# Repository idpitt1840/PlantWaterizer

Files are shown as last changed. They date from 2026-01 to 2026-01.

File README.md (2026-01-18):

An ESPHome / Home Assistant Indoor plant irrigation system

This unit monitors the moisture content of up to 5 plant pots and delivers water to them as needed.  It uses low cost moisture sensors and pumps. 



( The controller is the top box.  The bottom box is an overengineered grow light power switch that's repurposed from a different project ).



The pots are fed via a 3D printed water distribution ring ( STLs available from https://www.printables.com/model/103003-drip-irrigation-ring ). I modified the design a little to take a bigger hose.



The pumps are held in a 5 gallon bucket, lid cutout is to prevent the cats from trying to get a drink and knocking the whole thing over.  The hoses are held in place with 3D printed mounts, STL at https://www.thingiverse.com/thing:5642735/files. The pumps are held at the bottom of the bucket simply by the friction of the hose clamps and the hose itself. I did create a 3D printed mount for all of this then decided not to stick more microplastics into the mix. 

Soil sensors are enclosed in a 3D printed housing, STL at: https://www.printables.com/model/247398-capacitive-soil-moisture-sensor-v20-cover

The project case is generated from the follow parametric OpenSCAD project: https://www.printables.com/model/72839-customizable-parametric-stable-and-waterproof-elec.    The hardware is probably overkill but it adds a nice industrial look to the finished project: 



( Yes, I know the Float and Water sensor labels don't match  the connectors ).  This unit is currently driving 4 zones.  I've included a 3MF 3d print project file for the labelled lid if you have  Prusa MMU unit for doing mulitple colors. 

Assembled unit: 





Plenty of hot glue to keep those connectors under control. The aviation plugs should be fine if tightened up sufficiently. The USB sockets were a little wobbly so they need the glue treatment.  The wires from the LEDs and connectors are soldered directly to the header pins which isn't great and makes for fiddly assembly. I really couldn't be bothered with creating the dupont connectors enmass.   The moisture sensor inputs require 3v3, input and ground connectivity. The onboard 3v3 regulator on the ESP32 devkit board has enough capacity for these.   The pumps are fed from 5V via the MOSFETs.  Are MOSFETS overkill? Probably but they work and I had them and there's zero heat given off due to the low voltages, currents and the fact they're not rapidly switching on and off plus if I choose to upgrade the pumps to high current units, I won't need to change the design. A common NPN transistor might do the job. 

While this design uses HomeAssistant for status reporting and dashboarding,  it will run standalone once flashed since the logic controlling the moisture is in the ESP32.  You'll need to set the timeouts on the network and Home Assistant API to 0 in the code if you wish to run standalone.
I use Home Assistant for emailing me when the water is low and manual control of the pumps, and the dashboarding of course.   HA also controls the grow lights, though as a simple timer. 

When I added up all the components, it came to a somewhat shocking $100+ USD though a lot of that is due to the connecting hardware.  That's still way cheaper than having a 5 zone commercial unit though.  Costs can be saved in the connection hardware. The controller board itself probably tops out at around $25 with the main cost coming from the ESP32 and the MOSFETs, at least a hobbyist levels of purchasing power. 

The pumps aren't great. They are only $2 each so I'm not surprised. They have just enough water column head capacity to do what I want though one of the pots is right on the edge given it's height.  If you look in the code, you'll see one zone waters on a longer on cycle than the others. That's for this pot. I didn't do any noise or spike supression of the motor power circuits since I figured they were USB only and that would be within the motor.  I did find that the float switch GPIO would occasionally trigger when a pump turned on but I solved that through software. 

A note on the ESP32-S3 devboard: You could get away with a simpler ESP32 device since the S3 is overkill for the needs of this unit.  Note that the footprint in the schematic isn't quite the same as the board I used with the only difference of note being the ADC inputs. The ADC inputs you use isn't that important, though look to keep within the ADC-1 range rather than ADC-2 since that gets used for the chip's wifi apparently.  Just update the YAML for ESPHome accordingly. While this board has PSRAM, the program doesn't use it.  I really should have just used a cheaper board :) 

The board layout was done in KiCad.  I used Gemini to create some python to generate the strip board layout since that then allowed me to print the cutting mask to stick on the underside of the strip board for guiding my track cutting hand. It also allowed for a 3D representation to be rotated and zoomed to check that it was buildable. I had tried Fritzing which, while very capable, didn't have the fabrication tools that KiCad with python allowed me to have. I've uploaded the KiCad folder should you wish to go this route.  I added a screen shot of the strip board layout anyway. 

Enjoy

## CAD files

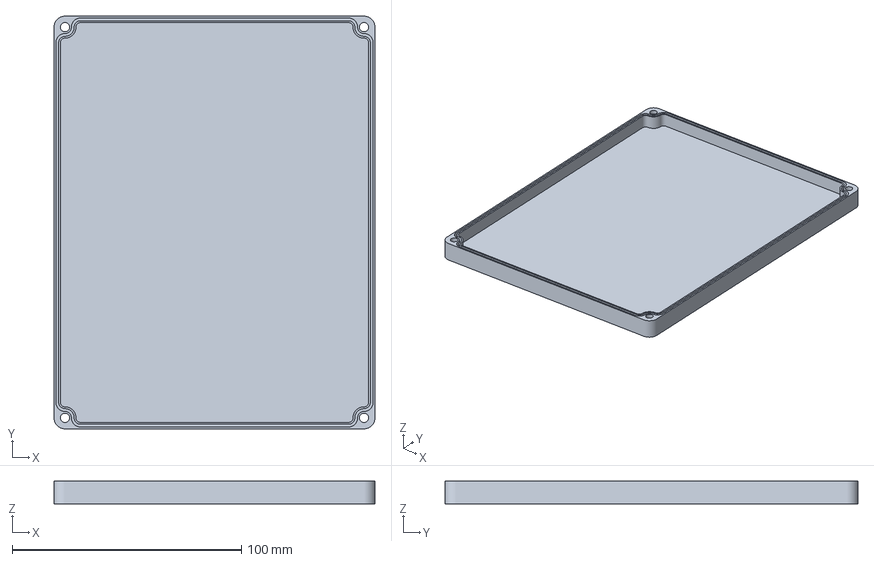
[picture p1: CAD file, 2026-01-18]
case/top-water-ultimatewaterproofcase_v74.3mf
140.0 x 180.0 x 10.0 mm

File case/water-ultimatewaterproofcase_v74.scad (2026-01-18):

/*******************************************************************************
TITLE:
Stable and waterproof OpenSCAD case by pbtec

DESCRIPTION:

highly scalable case for 3D printing. Try it out!

Optimized for Openscad Customizer. Activate it under view/customizer and play around ;-)

No Support needed to print

- for waterproof cases you can use silicone sealing cord with diameters from 1 to 3mm
- to use also without sealing cord. The groove and ridge gives the housing a high stability and tightness.
- Use of Hot melt copper nuts, regular nuts or square nuts
- define outer vertical radius of corners
- echo output in console shows inner and outer size and more
- echo output shows the needed length of the screws
- use screws from m2 up to m5
- default are 4 screws at each corner. For large cases add addtional ones in the middle of both x and y sides if needed
- use several predefined wall mount holder, some with multiple mounting holes (up to 3)
- the screw holes can now be configured to go through the case or not. The regular nut can also be moved to the bottom of the case
- custumizable 1 to 3 holes on each side for cable glands or similar
- holder for up to 3 pcbs or devices
- bottom mounting holes for wall mounting (not recommended for highly water-resistant housings)

Important!
- If you use standard nuts, you need to pause the printer a certain level to insert the nuts
- If you need a stable and waterproof case please print with 100% infill
- I am aware that sometimes, when using too big or too small parameters, there are some rendering issues.
  To prevent such issues change only one parameter at once and check the result.

for waterproofness see https://blog.prusaprinters.org/watertight-3d-printing-part-2_53638/

This work is licensed under a Creative Commons (4.0 International License)
Attribution-Noncommercial-Share Alike
not allowed | Sharing without ATTRIBUTION
allowed     | Remix Culture allowed
not allowed | Commercial Use
not allowed | Free Cultural Works
not allowed | Meets Open Definition

AUTHOR:
pbtec / pb-tec.ch

use https://paypal.me/pbtec if you want to spend me a coold beer. Thanks in advance :-)

VERSION:
V   KZZ DATE     COMMENT
6.0 pb  31.07.21 First Version to share
6.1 pb  15.12.22 Fixed some problems with german characters (Umlaute) in the code
7.0 pb  15.03.25 Added the option to use hot melt copper nut inserts
7.1 pb  16.03.25 Added solution for 3 pcb holders and 3 side wall holes on each side
7.2 pb  16.03.25 Added separate gasket option to print it with flexible material like TPU
7.3 pb  18.04.25 Fixed again some special character in the comments preventing the code to run
7.4 pb	02.05.25 Crazy, I found unexpected characters (-) on line 36, which turned out to be the issue.

*******************************************************************************/

/* [Render quality settings] */
// Set to at least to 150 before render and save as .stl file, otherwise you can go down to 40 for quick 3D view
$fn                       = 80;   // [20:1:300]

/* [View settings] */
// Shows the Bottom of the case
ShowBottom                = true;
// Shows the top of the case
ShowTop                   = true;
// Distance between top and bottom (if both are side by side displayed)
DistanceBetweenObjects    = 10;
// Shows the housing assembled
ShowCaseAssembled         = false;
// Shows the gasket
ShowGasket                = true;
GasketHeight                = 1.5;

/* [Control cuts (use only one at a time)] */
// To see the nuts inside (best view if not assembled showed)
SeeNutCut                 = false;
// To see the groove, ridge and Screw (best view if assembled showed)
SeeGrooveRidgeScrew       = false;

/* [Case settings] */
// Length of the case
Caselength                = 60;
// Width of the case
CaseWidth                 = 100;
// Height of the case
CaseHeight                = 40;
// Splitt the Case height into bottom and top, check for the needed screws in echo output (console)
CutFromTop                = 10.0;
// Thickness for the bottom and top wall (vertical walls needs to be calculated)
BottomTopThickness        = 3.0;
// If this is bigger than the needed cylinder around the screw it will be ignored
CaseRadius                = 12.0;

/* [Groove settings] */
// If using a SealingCord use the SealingCord diameter, otherwise x-times of your 3D Printer Nozzle (0.8/1.2/...) --> Ridge gets perfect for printing
GrooveWidth               = 1.2;   // [0.8:0.1:3]
// Not less than 1mm (for stability) and not more than 3mm --> Best 2mm
GrooveDepth               = 2.0;   // [1.0:0.1:3]
// Space between Groove and Ridge for a perfect fit, usualy 0.2 or 0.3 for FDM depending on your printer quality
Space                     = 0.3;   // [0.0:0.1:0.4]
// Addtional vertical room for the pressed sealing Cord. For sealing cord 1.5mm -->0.5 // for 2mm -->0.8 // for 2.5 -->1.0 // If no sealing cord then set this parameter to 0.
AddGrooveDepthForSealing  = 0.8;   // [0.0:0.1:3]
// Range Inside groove/ridge. Usualy 2 times or more the printer nozzle. For best stability at least 0.8
InnerBorder               = 0.8;   // [0.8:0.1:4]
// Range Outside groove/ridge . Usualy 2 times or more the printer nozzle. For best stability at least 0.8
OuterBorder               = 0.8;   // [0.8:0.1:4]

/* [Case Screw settings] */
//2=m2/2.5=m2.5/3=m3/4=m4/5=m5   // max m5, larger sizes do not fit
MetricScrewSize          = 3.0;     // [2:m2, 2.5: m2.5, 3: m3, 4: m4, 5: m5]
// Chose your Screw head
ScrewHeadType            = 1;      // [1:1 Countersunk head screw, 2: 2 Round or hex screw head - Counterbore, 3: 3 Exposed head - No counter]
// for round or hex screw head select the height of the head
ScrewHeadHeight  = 2.6;   // [0.0:0.1:10]
// for round head screw select the diameter of the head, for hex screw select the diameter size of your Socket wrench diameter
ScrewHeadDiameter  = 6;   // [0.0:0.1:20]
// Screw or hot melt nut Hole deepness (deepness in the Body/Cylinder). If too big, through hole possible
HoleDeepness              = 20.0 ; //[1:0.1:500]
// Adds additional Screws on X axis (for large cases) --> Try it out
XAdditionalScrew          = false;  // can be true or false / Adds additional Screws on X axis (for large cases) --> Try it out
// Adds additional Screws on Y axis (for large cases) --> Try it out
YAdditionalScrew          = false;  // can be true or false / Adds additional Screws on Y axis (for large cases) --> Try it out

/* [Nut general settings] */
NutStyle          = 1;      // [1:1 Hot melt copper nut > New from Version 7.0, 2: 2 Standard nuts > Pause during printing to insert standard nuts, 3: 3 Square nuts > Pause during printing to insert square nuts, 4 : 4 Square nuts with external insert > No need for pause during print - but outer holes are visible]
// Size of material (plastic) above nut/square nut (3mm or better more). Use for NutStyle 2,3 and 4). The more, the more stable but need longer screws. Here you can also move the nut to the bottom of the case (since Version 7.0)
NutSink                   = 4.0; // [0:0.1:500]


/* [Hot melt copper nut settings (use for NutStyle 1) can also be used for self-tapping screws] */
// Hole diameter for self-tapped screw or hot melt copper nut (Measure the diameter))
HoleDiaThread             = 3.2 ; //[1:0.1:10]
// Length of the hot melt copper nut (Measure the length) - It is just used to calculate the min length of the screw to output in console
HolelengthHotMeltNut      = 10 ; //[1:0.1:30]

/* [Standard nut settings (use for NutStyle 2)] */
// Nut Settings / As there are (or I have) many different nuts dimensions, the size must be specified / Do not add separation space, only the real measurement // m2=1.5 // m2.5=1.9 // m3=2.4 // m4=3.2 // n5=3.8
NutHigh                   = 2.4;
// Distance between the paralell sides / Do not add separation space, only the real measurement // m2=3.8 // m2.5=4.9 // m3=5.4 // m4=6.9 // m5=7.9
NutDia                    = 5.4;

/* [Square Nut settings (Use for NutStyle 3 + 4)] */
// Select the high of the square nut / Do not add separation space, only the real measurement
SquareNutHigh             = 1.9;
// Select the size of the square nut / Do not add separation space, only the real measurement
SquareNutSize             = 5.4;
// Square nut insert from which side (NutStyle 4 only)
EdgeSquareNutInsertFrom_X = true;

/* [Wall mount holder settings] */
// Select if you need a mount holder
EnableMountHolder         = false;
// Chose your desired wall mount style
MountHolderStyle          = 5;      // [1:Style 1, 2: Style 2, 3: Style 3, 4 : Style 4, 5 : Style 5]
// Some styles (1-3) allow more than one hole
CountOfMountHolderHoles   = 1;     // [1:One hole centered, 2: Two holes, 3: Three holes]
MountHolderHoleDiameter   = 5;   // [1:0.1:10]
MountHolderThickness      = 4.0;   // [2:0.1:10]
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

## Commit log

2026-01-18 Add initial configuration for PlantWaterinator
    This configuration file sets up the PlantWaterinator system using ESPHome, defining sensors, switches, and scripts for automated plant watering.
2026-01-18 Create KiCad
2026-01-18 Enhance README with detailed project descriptions
    Expanded descriptions of the water distribution ring and pump setup, including modifications and additional details about 3D printed mounts.
2026-01-18 Update README with new image and assembly details
    Added an additional image and updated assembly notes in the README.
2026-01-18 Add files via upload
    A PrusaSlicer 3MF file that contains the labelling on the lid if you have an MMU.
    [top-water-ultimatewaterproofcase_v74.3mf]
2026-03-17 Update Bill of materials with new pump model
    Added new pump model that works well with greater head capacity.
